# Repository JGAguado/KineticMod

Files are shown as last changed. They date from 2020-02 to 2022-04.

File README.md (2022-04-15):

[][releases]
[](LICENSE)

[][maintenance]
[][buymecoffee]

# KineticMod
Mod for ArduLab, directly plugable via the Mod Interface. The KineticMod is designed to enhance the ArduLab functions applied to control multiple motors by PWM such as servos.

<p float="left">
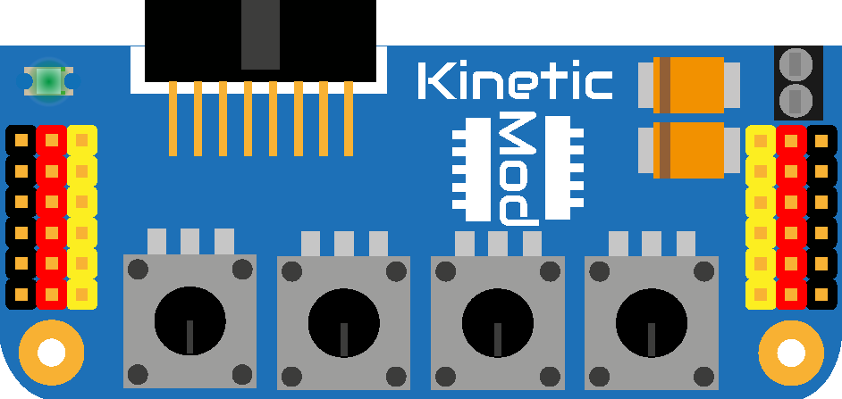
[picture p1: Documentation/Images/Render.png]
   
</p>

## Project tree

<li><a href="./Design/">Design</a></li>
<li><a href="./Documentation/">Documentation</a></li>

<li><a href="./README.md">README.md</a></li>

[releases-shield]: https://img.shields.io/github/release/JGAguado/KineticMod.svg?style=for-the-badge
[releases]: https://github.com/JGAguado/KineticMod/releases

[license-shield]: https://img.shields.io/badge/License-CC%20BY--NC--SA%204.0-lightgrey.svg?style=for-the-badge

[maintenance-shield]: https://img.shields.io/badge/maintainer-J.%20G.%20Aguado-blue.svg?style=for-the-badge
[maintenance]: https://github.com/JGAguado

[buymecoffee-shield]: https://img.shields.io/badge/buy%20me%20a%20coffee-support-yellow.svg?style=for-the-badge
[buymecoffee]: https://www.buymeacoffee.com/J.G.Aguado

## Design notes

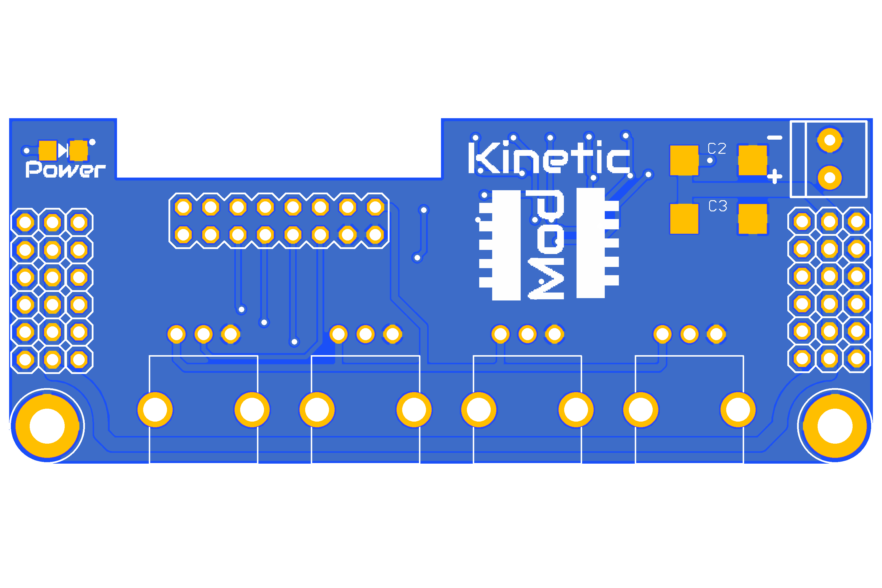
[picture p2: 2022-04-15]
Documentation/Images/Top.png

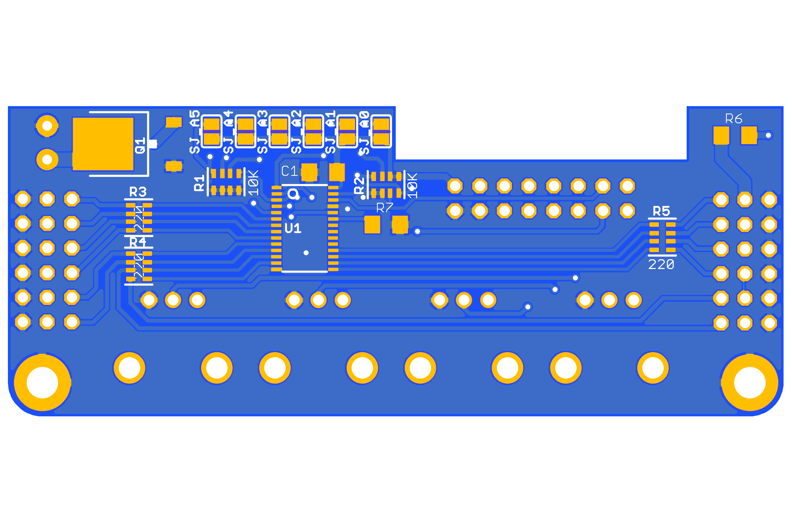
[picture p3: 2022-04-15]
Documentation/Images/Bottom.png

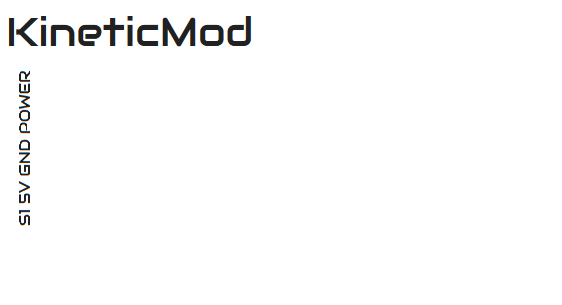
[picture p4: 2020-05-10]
Documentation/Silkscreen/Title.PNG

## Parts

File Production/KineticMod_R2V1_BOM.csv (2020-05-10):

No. | Design Ref | Description | Value | Package | Qty | Notes
1 | C1 | Capacitor | 10 uF | C1206 | 1
2 | C2 | Polarized capacitor | 1000 uF | 7343 | 1 | Mouser No: 581-TAJE108M006RNJ
3 | L1 | Led | Green | 1206 | 1
4 | Q1 | Mosfet P-CH 30V | AOD417 | TO252 | 1 | https://www.digikey.es/product-detail/es/alpha-omega-semiconductor-inc/AOD417/785-1106-1-ND/1856049
5 | R1, R2 | Resistor array 4 resistor | 10K | 603 | 2 | Mouser No: 667-EXB-38V103JV
6 | R3, R4, R5 | Resistor array 4 resistor | 220 | 603 | 3 | Mouser No: 667-EXB-38V221JV
7 | R6 | Resistor | 470 | R1206 | 1
8 | R7 | Resistor | 10K | R1206 | 1
9 | SV1 | Pin header 2,54 - Right Angle | SFH11-PBPC-D08-RA-BK |  | 1 | Sullins Part No: SFH11-PBPC-D08-RA-BK
10 | U1 | Controlador IC 16 Salida Lineal PWM | PCA9685 | TSSOP28 | 1
11 | JP1, JP2 | Pin header 2,54 - Vertical | 1x6 | Black | 2 | Soldered on Top layer in the column "-"
12 | JP3, JP4 | Pin header 2,54 - Vertical | 1x6 | Red | 2 | Soldered on Top layer in the column "+"
13 | JP5, JP6 | Pin header 2,54 - Vertical | 1x6 | Yellow | 2 | Soldered on Top layer in the column "S"
14 | JP7 | Terminal block 3.5mm | 1x2 | Through Hole | 1 | https://www.digikey.com/product-detail/en/amphenol-anytek/T50201500000G/T50201500000G-ND/4940066
 |  |  |  |  | 12

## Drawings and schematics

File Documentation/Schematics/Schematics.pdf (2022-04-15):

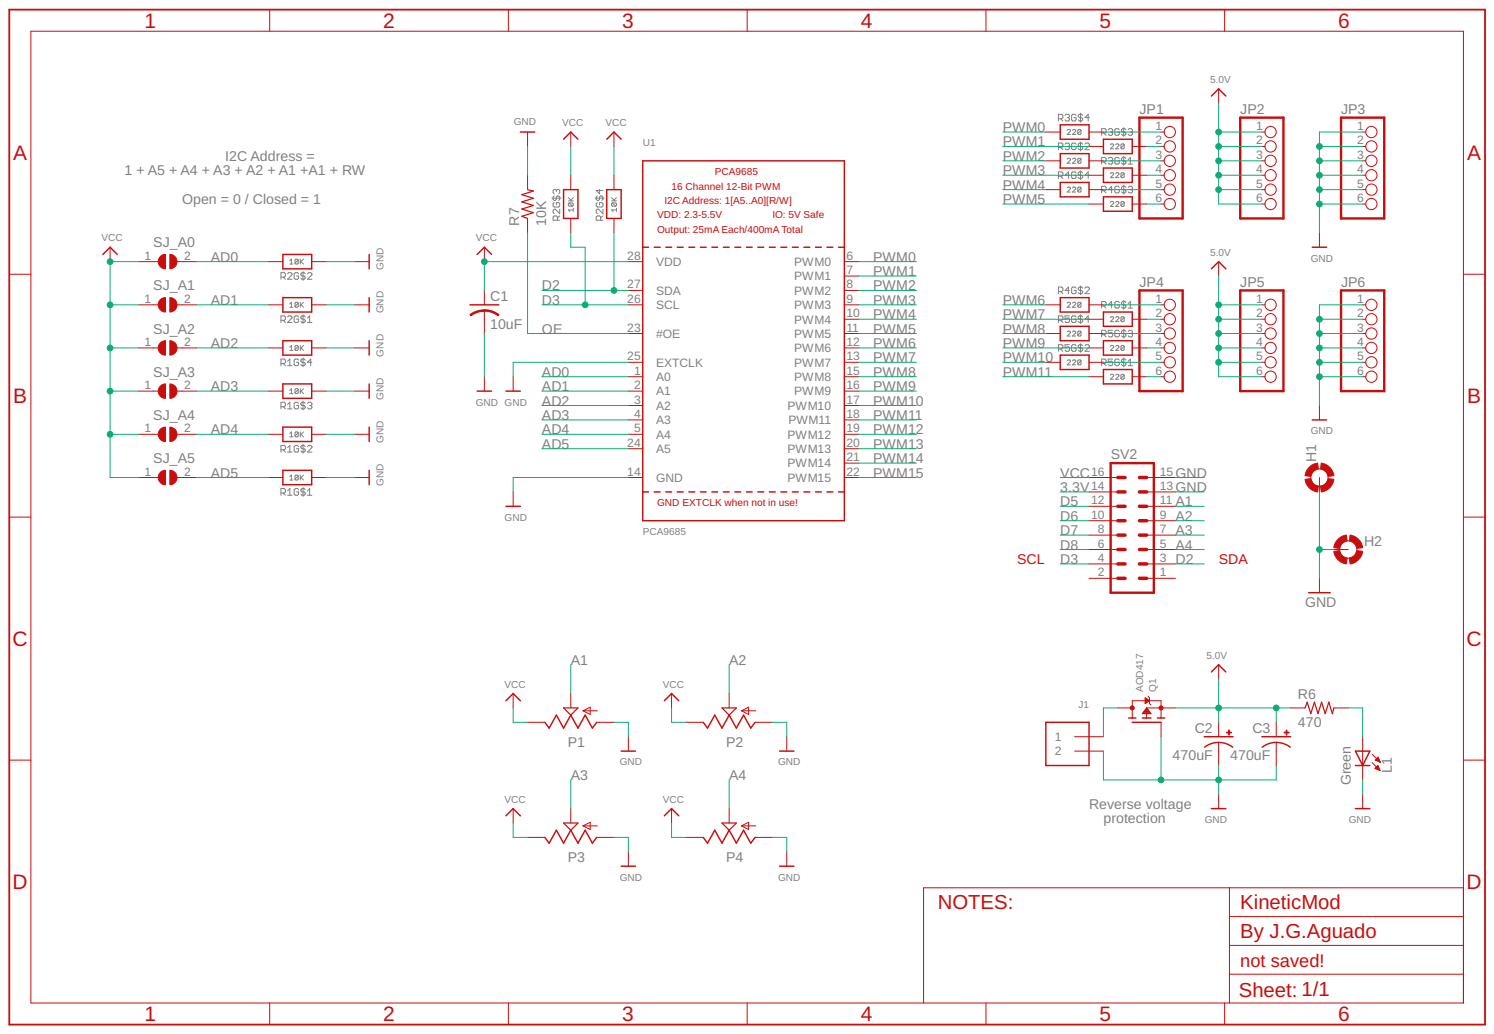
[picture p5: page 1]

GND GND GND GND GND GND GND

GND EXTCLK when not in use!

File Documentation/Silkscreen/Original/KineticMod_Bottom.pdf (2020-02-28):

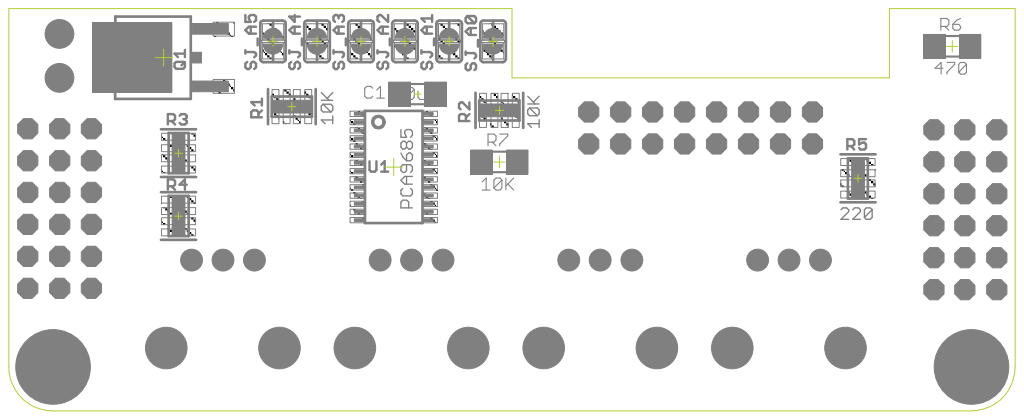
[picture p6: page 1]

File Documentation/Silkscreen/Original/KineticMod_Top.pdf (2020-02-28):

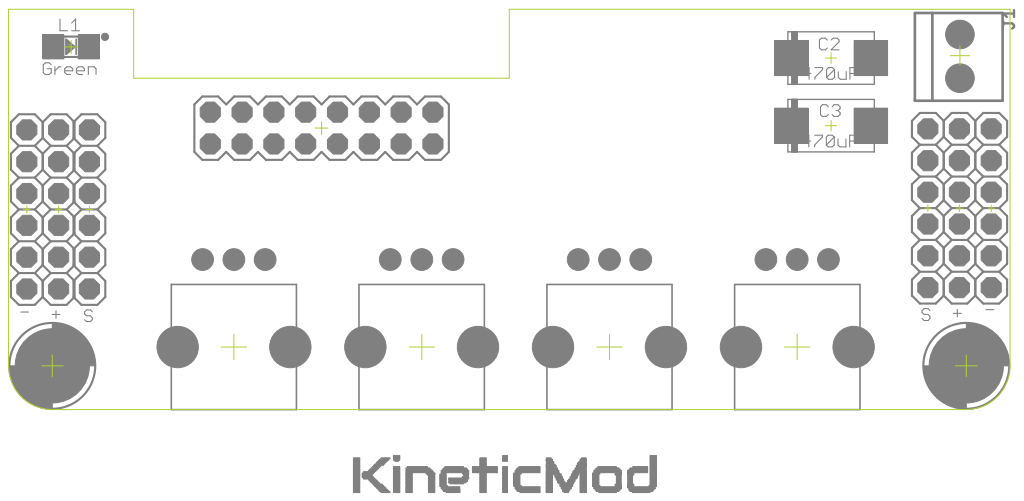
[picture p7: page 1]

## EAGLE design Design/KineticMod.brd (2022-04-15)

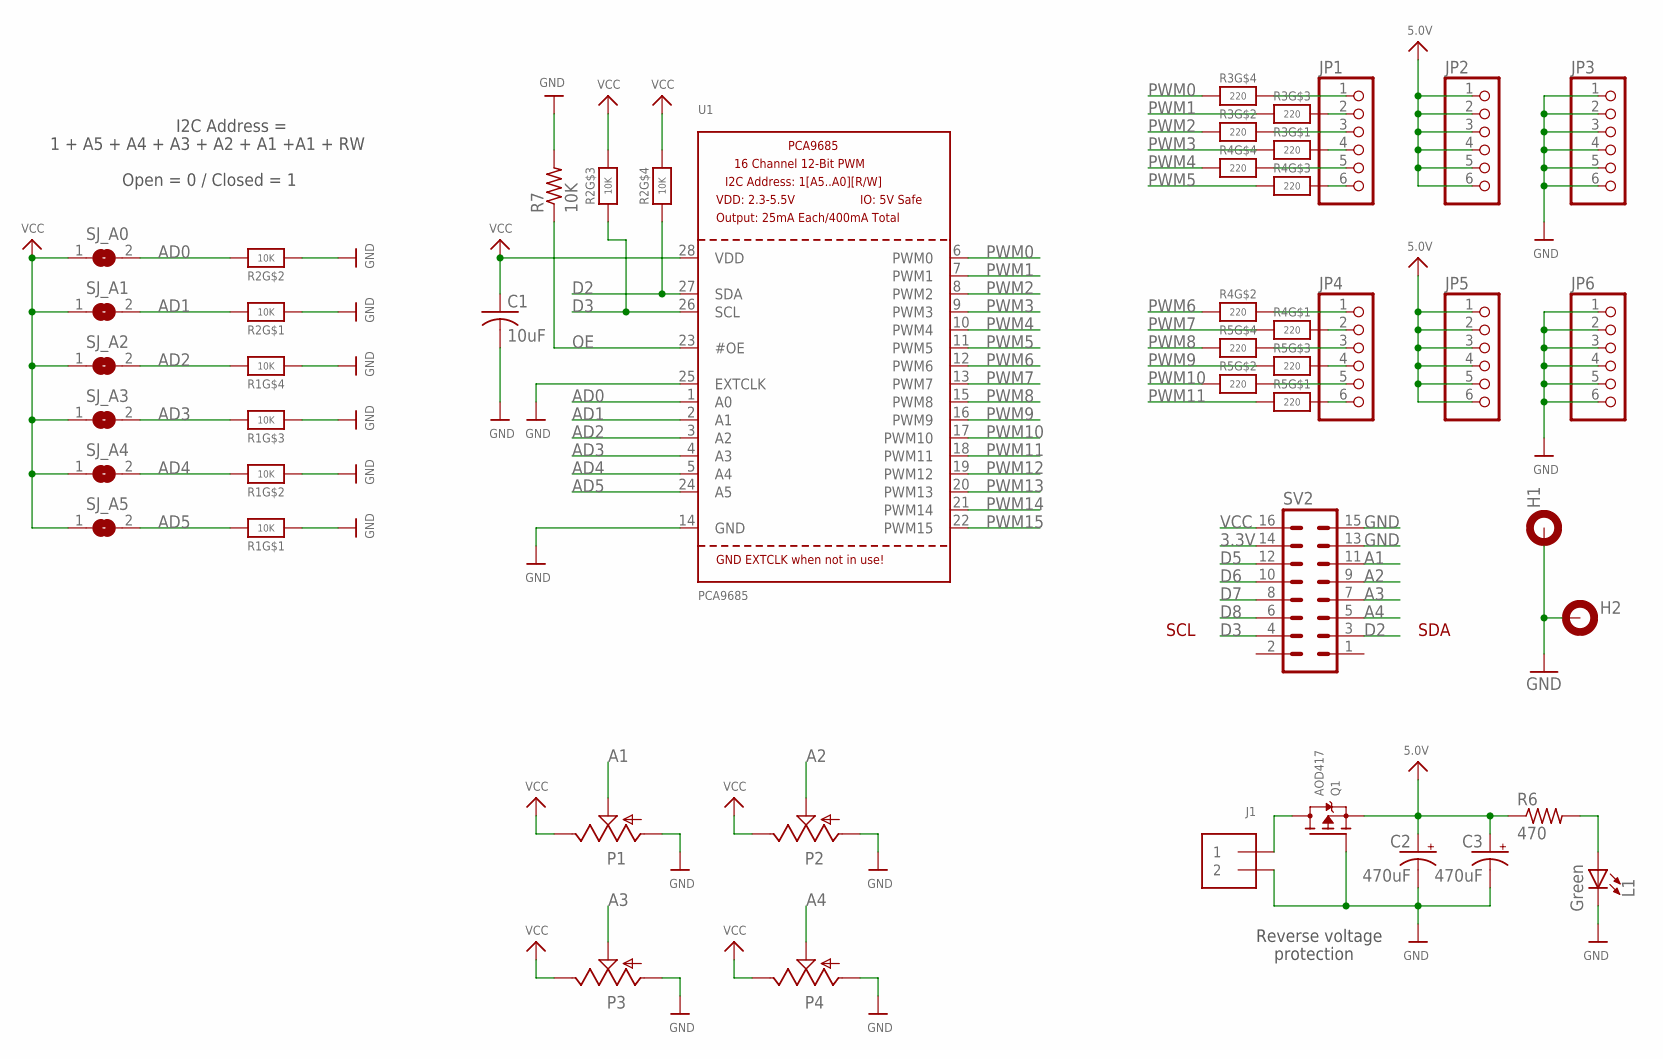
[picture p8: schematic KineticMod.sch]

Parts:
C1: 10uF; 1206
C2, C3: 470uF; D/7343-31R
H1, H2: MOUNT-PAD-ROUND3.2; 3,2-PAD
J1: TERMBLOCK_1X2; TERMBLOCK_1X2-3.5MM
JP1, JP2, JP3, JP4, JP5, JP6: PINHD-1X6; 1X06
L1: Green; LED1206
P1, P2, P3, P4: ALPS_RK09K_VERTICAL
Q1: AOD417; TO252
R1, R2: 10K; RESPACK_4X0603
R3, R4, R5: 220; RESPACK_4X0603
R6: 470; 1206
R7: 10K; 1206
SJ_A0, SJ_A1, SJ_A2, SJ_A3, SJ_A4, SJ_A5: SOLDERJUMPERREFLOW_NOPASTE; SOLDERJUMPER_REFLOW_NOPASTE
SV2: MA08-2
U1: PCA9685; TSSOP28

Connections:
3.3V: SV2.14
5.0V: C2.+, C3.+, JP2.1, JP2.2, JP2.3, JP2.4, JP2.5, JP2.6, JP5.1, JP5.2, JP5.3, JP5.4, JP5.5, JP5.6, Q1.2 (S), R6.1
A1: P1.2, SV2.11
A2: P2.2, SV2.9
A3: P3.2, SV2.7
A4: P4.2, SV2.5
AD0: R2.7 (2), SJ_A0.2, U1.1 (A0)
AD1: R2.8 (2), SJ_A1.2, U1.2 (A1)
AD2: R1.5 (2), SJ_A2.2, U1.3 (A2)
AD3: R1.6 (2), SJ_A3.2, U1.4 (A3)
AD4: R1.7 (2), SJ_A4.2, U1.5 (A4)
AD5: R1.8 (2), SJ_A5.2, U1.24 (A5)
D2: R2.4 (1), SV2.3, U1.27 (SDA)
D3: R2.3 (1), SV2.4, U1.26 (SCL)
D5: SV2.12
D6: SV2.10
D7: SV2.8
D8: SV2.6
GND: C1.2, C2.-, C3.-, H1.B3,2, H2.B3,2, J1.2, JP3.1, JP3.2, JP3.3, JP3.4, JP3.5, JP3.6, JP6.1, JP6.2, JP6.3, JP6.4, JP6.5, JP6.6, L1.C, P1.1, P2.1, P3.1, P4.1, Q1.1 (G), R1.1, R1.2 (1), R1.3 (1), R1.4 (1), R2.1, R2.2 (1), R7.2, SV2.13, SV2.15, U1.14 (GND), U1.25 (EXTCLK)
unnamed: L1.A, R6.2
unnamed: JP4.1, R4.7 (2)
unnamed: JP4.2, R4.8 (2)
unnamed: JP1.6, R4.6 (2)
unnamed: JP1.5, R4.5 (2)
unnamed: JP1.4, R3.8 (2)
unnamed: JP1.3, R3.7 (2)
unnamed: JP1.2, R3.6 (2)
unnamed: JP1.1, R3.5 (2)
unnamed: JP4.3, R5.5 (2)
unnamed: JP4.4, R5.6 (2)
unnamed: JP4.5, R5.7 (2)
unnamed: JP4.6, R5.8 (2)
OE: R7.1, U1.23 (#OE)
PWM0: R3.4 (1), U1.6 (PWM0)
PWM1: R3.3 (1), U1.7 (PWM1)
PWM2: R3.2 (1), U1.8 (PWM2)
PWM3: R3.1, U1.9 (PWM3)
PWM4: R4.4 (1), U1.10 (PWM4)
PWM5: R4.3 (1), U1.11 (PWM5)
PWM6: R4.2 (1), U1.12 (PWM6)
PWM7: R4.1, U1.13 (PWM7)
PWM8: R5.4 (1), U1.15 (PWM8)
PWM9: R5.3 (1), U1.16 (PWM9)
PWM10: R5.2 (1), U1.17 (PWM10)
PWM11: R5.1, U1.18 (PWM11)
PWM12: U1.19 (PWM12)
PWM13: U1.20 (PWM13)
PWM14: U1.21 (PWM14)
PWM15: U1.22 (PWM15)
PWRIN: J1.1, Q1.3 (D)
VCC: C1.1, P1.3, P2.3, P3.3, P4.3, R2.5 (2), R2.6 (2), SJ_A0.1, SJ_A1.1, SJ_A2.1, SJ_A3.1, SJ_A4.1, SJ_A5.1, SV2.16, U1.28 (VDD)

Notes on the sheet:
SCL
SDA
Reverse voltage
protection
1 + A5 + A4 + A3 + A2 + A1 +A1 + RW
I2C Address =
Open = 0 / Closed = 1

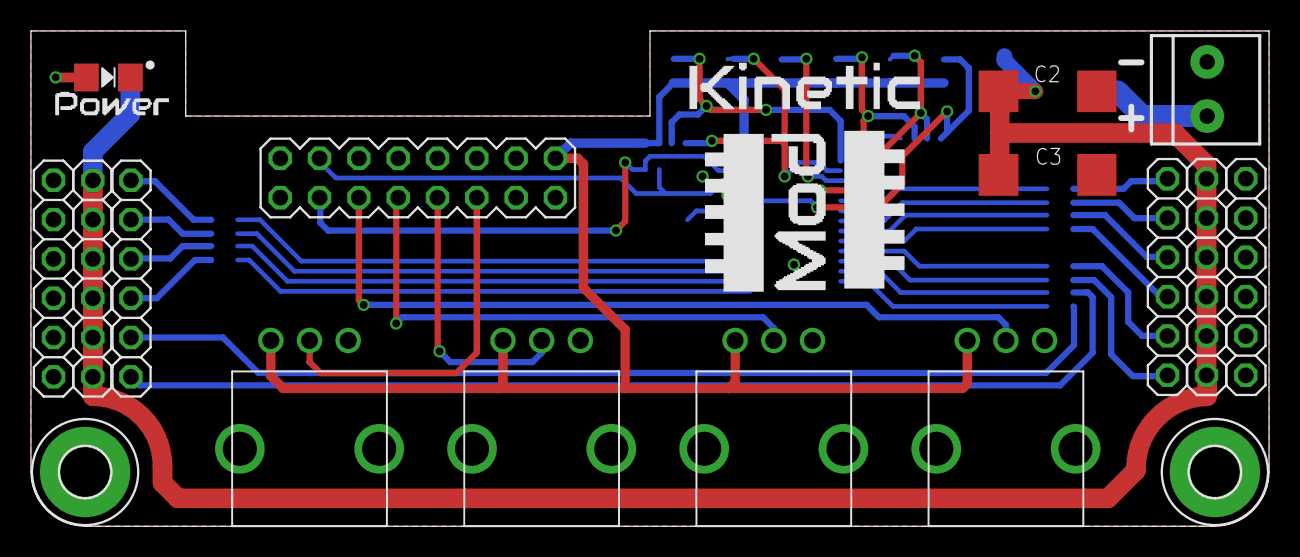
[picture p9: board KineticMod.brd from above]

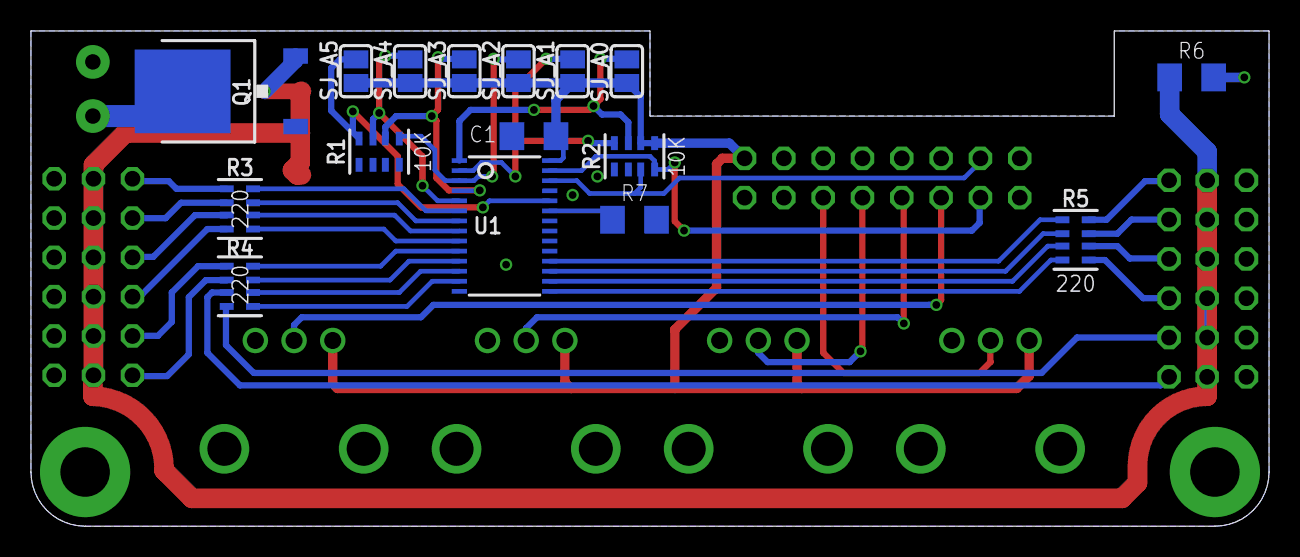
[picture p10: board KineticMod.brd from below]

Board: 2 copper layers, 80.0 x 32.0 mm, 33 parts (16 on the bottom side), 42 nets.

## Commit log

2018-04-30 Initial commit KineticMod. Added SCH and BRD files
    [KineticMod.brd, KineticMod.sch]
2020-01-23 Updated KineticMod
    [KineticMod.brd, KineticMod.sch]
2020-02-28 Updated capacitors: - C2 replaced by 470uF 2917 (7343) - Added C3 470uF 2917 (7343)
    Updated silkscreen
    [KineticMod.brd, KineticMod.sch]
2020-02-28 Silkscreen original
2020-05-10 Updated Hardware design
    [KineticMod.brd]
2020-05-10 Update silkscreens
2020-05-10 Updated Production files
    [KineticMod_R2V1_2_Centroid.csv, KineticMod_R2V1_BOM.csv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]
2022-04-15 Updated structure
    [KineticMod.brd, KineticMod.sch]
